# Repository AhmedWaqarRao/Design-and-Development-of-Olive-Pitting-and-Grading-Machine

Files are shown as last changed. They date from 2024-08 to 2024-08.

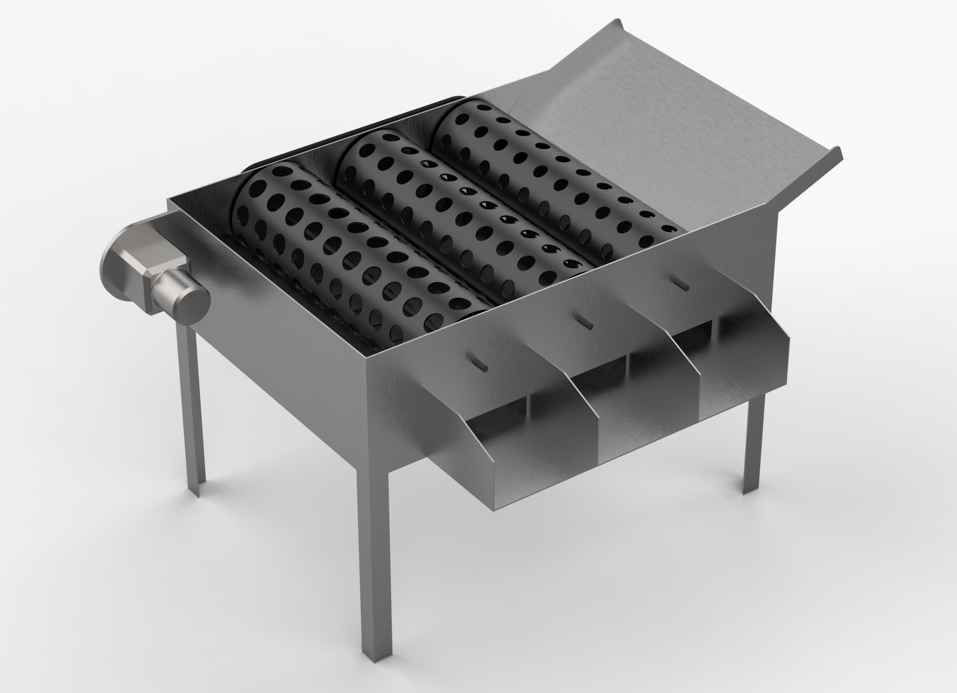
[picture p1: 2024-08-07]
Render 2 final design.png

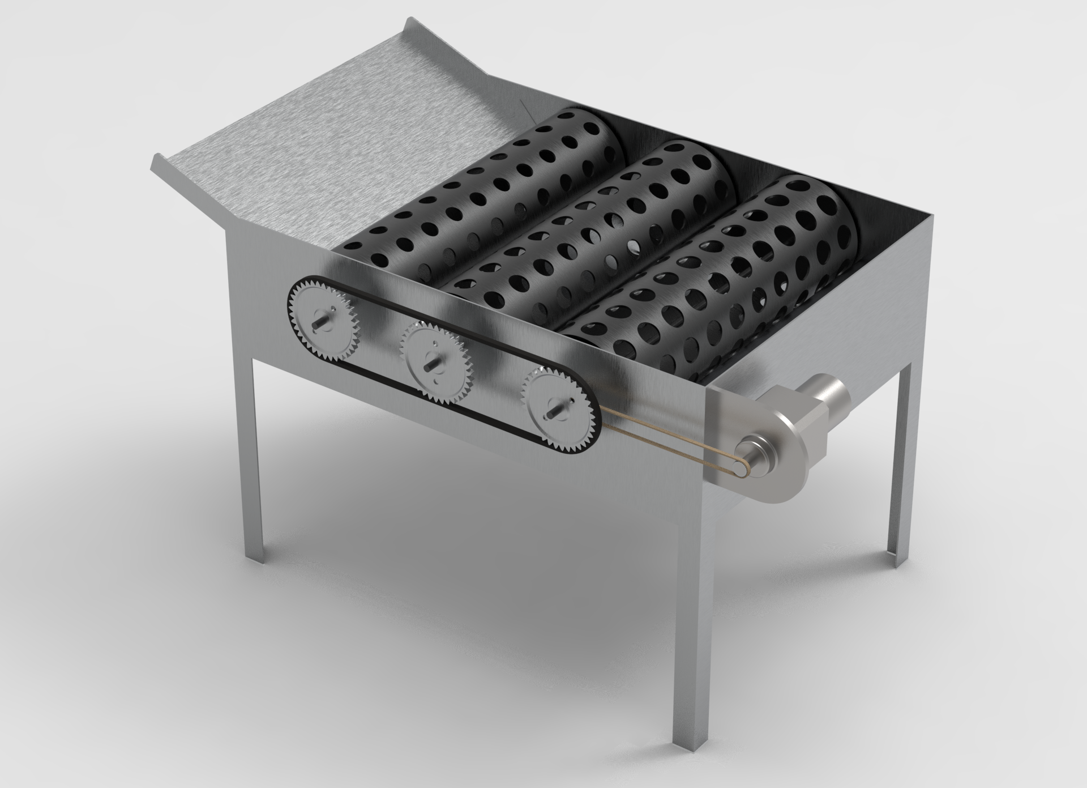
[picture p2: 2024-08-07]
Render final design 1.png

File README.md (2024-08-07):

# Design-and-Development-of-Olive-Pitting-and-Grading-Machine
An opportunity provides an effective mechanism for the purpose of the olives and removing pits from the
various varieties of olives cultivated in Pakistan. The project mainly focuses on the 3D model & hardware of
the Grading Mechanism of olives and the 3D CAD model of the pitting machine.75% of olive oil is imported
annually for domestic consumption.
The output will be a semi-automated machine that can grade and pit a number of olives at a time and has
an industrial and commercial approach.
A grading Mechanism will be used for the partition of different quality olives based on Olives.
Remove the seeds of olives when placed inside the Olive carrier drums along with the pins with the
help of two mechanisms.
i.e 1. Geneva Mechanism 2. Slider Crank Mechanism.

Final Year Project
— The invention in the technological world in Olive processing industry which increases the demand of the Olive industry. Olive pitting machine is mainly used for crushing and pitting of olives. The destoning of olive is the major area of concern in this project. A prototype is designed known as semi-autonomous machine for the extraction of olive and pitting process. Our Project is mainly focus on the Design of the Olive pitting Machine & Grading Machine. 
This machine will operate on no of mechanisms such as Geneva and slider crank mechanism. The assembly of machine is designed keeping in mind that all sizes of olives can be placed in one go on which pitting process need to be carried out. The major concern of our project lies in passing olives through fruit grading machine and then after this put that passed Olive into the Olive Pitting Machine whose task is to remove the seeds or pits of olives successfully the without damaging the outer part of the fruit.
 The project we have chosen for our FYP has both commercial and industrial value. The project holds to remove pit from olives mesh and then these olives can serve application in foods we are used on daily basis like tables olives, pickled olives and for extracting olives oil. Our area of target is to design a prototype whose specifications is grading olive one their sizes and destoning of pits.
I.	Introduction
Olive industry is growing day by day with the in interventions of technological solutions in olives process industry. The project holds to remove pit from olives mesh and then these olives can serve application in foods like tables olives and oil can also be extracted from the oils and is also used in pickels. We are to design a semi-automated machine whose function is to remove pit form olives [1].
There are 3 major parts in this semi-automated machine i.e., Olive feeder, Olive carrier, Pit detaching device. Olive feeder is the only semi-automatic part of the machine. In olive feeder olives need to be placed in such a way that it is in perfect contact with tip of needle and needle strike them longitudinally. 

Olive carrier is a revolving drum with sockets to hold various sizes of olives in predetermined position. The 24V motor is needed to rotate this drum and when needle encounter olive means when it strikes the olive then drum stop rotating. Pit detaching device consists of system of 9 needles which is capable of destoning 9 olives in just one go. The invention in the technological world in Olive processing industry which increases the demand of the Olive industry [3].

Olive pitting machine is mainly used for crushing and pitting of olives [2]. Our Project is mainly focus on the Design of the Olive pitting Machine & Grading Machine. The major objective of the of this project first to pass the olive through the Grading Machine and then after this put that passed Olive into the Olive Pitting Machine which successfully remove the pit of the olives without fracturing the outer part of the fruit [4]. The pitted Olive fruit can give us the income generating tool by making olive table oils, pickled olive and sliced or chopped olives can be use on pizza etc.

The Selected design of the Olive Extracting Machine resembles the cherry machine with modification in the driving mechanism having a Geneva Mechanism Crank-Slider Mechanism for the head of the device with a pitting needle. Holes of Rollers are selected according to the Grade of Olives needed to be pitted after being graded by the Olive Sorting Machine. 
The Pitting Machine Also includes Feeder and Collector Assembly for Feeding and collecting olives, respectively [5]. Mechanical System Based Olive Sorting: Mechanical based system for olive grading is the most used methodology. Mechanical Sorting Consists of Feeder Assembly through which olives are sent to conveyor belts arranged so that they are hollow from the bottom and carry the olives while moving forward.

II.	Methodology
Important paramteres and calculations
A.	DEVELOPMENT PHASE OF PITTING & GRADING MACHINE COMPONENT SPECIFICATIONS

	The overall parameters of the olive hopper, grading drums with holes; the length and diameters of drums, diameter and total number of holes and exit fall of the development grading-machine are included as follows.

B.	FINAL 3D CADCAM MODEL
This is the final achieved 3D CAD model of olive grading mechanism, after assembling all the parts. We entered the olives in 3 stages. First, we put 5kg of olives then 10kg and in 3rd stage we put 15kg of olives in the hopper, by 220 volts motor placed on the other side of the machine, the rolling drums starts to roll. 

Respective olives fall in 3 different categories according to their diameters which varies from 19mm diameter to 29mm.

After combining various mechanisms and components, the entire assembly of Olive Pit Extractor machine is obtained.
The shaft of the prime mover in the Geneva mechanism is connected to the crank in the slider crank mechanism.

The primary mover's wheel will be turned by an AC induction motor. The crank would generate rotational motion, which would be transformed into linear motion by the slider. The needle box is attached to the slider, and when linear motion is produced, the needle box moves along with the slider to conduct pitting operation.

 When the shaft of the prime mover catches on the slot of the driven wheel, it rotates the roller drum 45 degrees and aligns the roller drum sockets with those of the needle box for correct olive pitting.

Final 3d Cad Model Of Gradig Machine

Final 3d Cad Model Of pitting Machine

        C) Food Grading by Computer Vision:

In this modern era of industrialization, computer vision has become the most influential factor in revolutionizing the food industry. Food grading, including the size, orientation, Volume, weight, color, and checking the quality of a particular food type, has become very easy using computer vision. Machine Learning and Machine Vision make the perfect artificial intelligence system used for food processing. [10]

 1) Working:
 The most used Computer Vision Grading of Olives include    grading by Size and color. Modern image processing techniques are used to distinguish the difference in color and sizes. For imaging, High-Speed Cameras are used to capture images as fast as up to 120 frame rates.

 Data Acquisition Card (DAC) is used to control the system. Machine Learning is a must to process and compare the data to provide the best results. For color identification, Machine Learning techniques are used to easily differentiate between two colors that vary in intensities [11].

Figure : Olive Grading Machine Based on Machine Vision.

Figures : (a) Shows the machine’s interface (b) shows the high-speed cameras.

II.	SIMULATION ON ANSYS
To evaluate this design of machine it has been simulated and analyzed on different software named as Solid works and Ansys. Different set of analysis and constrained has been performed on machine.

A.	ANSYS SIMULATIONS:
1)	Static structural Analysis of Grading Machine:
Roller drum tis subjected to different simulations and the result shows that design of base of grading machine so strong and robust [6]. The Mild steel has Young Modulus of 2.10 x 10^9 pascal, which is used in manufacturing of needle. The poison ratio is 0.40 and mesh size is 20 mm .Following are the analysis run on this mechanism to test its robustness.

ANSYS software is used to perform analysis on different parts of grading machine. Force being applied on the bottom plate of the machine, pressure being applied on the rolling drums after olives are placed for grading and fixed supports of the machine, the figures are as below

                           Fixed Support             Force on the bottom plate

2)	Simulation by load of 50N:

      1) Directional and total deformation on x-axis:
A deformation option that displays all our model's deformation results in three coordinates (X, Y, and Z).  We can examine the deformation result of your physical model in this direction by entering a coordinate (X, Y, or Z) in directional deformation.

The directional deformation in x axis is applied on the roller drums. 50N load was applied. The results shows that the stress is high, but it doesn’t exceed certain limit. The pictorial representation of the result is shown below:

                             (1)                                               (2)
                      1) Directional Deformation in X axis – 50N  
                      2) Total Deformation – 50N

Von Mises Stress and elastic strain:
The drum is subjected to elastic strain and von misses stress are analyzed. 50N loads were applied to the drum. The results prove that drum is within limit and there are no chances that it will fracture. The following pictures shows the result carried out:
   
Analysis of Von-Mises Stress 50N  Analysis of Elastic Strain – 50N

3)	Roller Drum Carriers of Olives:
Roller drums are used for converting rotary motion to linear motion of fruit from the delivery plate. The coupler link was subjected to different simulations. The material for coupler is stainless steel and with Young Modulus of 2.10x10^7 pa. The mesh size is 20mm and   poison ratio is 0.40. Following are analysis run on roller drums and complete structure of grading machine shows its robustness.
B.	Output of Machine:
The olive pitting and grading machine is simulated in SOLID WORKS for motion analysis. The analysis shows that it is capable of grade 3 lines in 40 sec. We can conclude that machine is capable of grade 40-50kg of olives under certain conditions after analyzing the result.

C.	FRUITS:
We will be discussing 2 types of olive crops in this study: “Ascolana and Arbequina”. An approx. of 100 olives were used in our study. We collected the olive to be tested from the farms in Barani Agriculture Research Institute, Chakwal. Then the measurements were taken of the selected olives.
D.	GRADING-MACHINE: 
Following figures shows us the different parts being used in the grading machine, schematic diagrams help us to understand the parts of the grading machine.  The parameters depicted on the diagram are essentially those that will be determined for olives because of this investigation, to alter the grading machine to perform efficiently with this fruit [8].
 
Top view of assembled machine

Side view of assembled machine

            Designed Grading:
  		 1)  The Revolving Drums
Three revolving drums are made up of volcanized steel with following parameters: Diameter 92mm, length 305 mm, spacing 6mm, thickness 4mm. The three grading-drums have holes of diameters are 20-, 25- and 30-mm number of holes are 156, 137 and 124. 
Iron metal-sheet of 330mm length, 457 mm width and 1.5 mm (14 gauge) of thickness was assembled above grading-drums spacing and bolted on two sides of fruit boxes. 

2)  Fruit output unit
The output unit is made up of volcanized steel with length of 457mm and width of 127mm. Three fruit cutoffs were inserted into the three grading drums and fixed to the left side of the frame. The fruits slide down the concave surface of the output unit and fall into funnels. The curved section prevents fruits from being jammed. The inclined angle of output unit calculated is 12 degrees.

1)	Motor and Transmission System:
                     The grading system consists of 0.04 HP 	motor installed   and chains are given below:

 Chains side view of assembled machine

[1]
2)	1 Olive hopper:

The top dimensions are of 350 x 330 mm and bottom dimensions of 350 x 80 mm. The frictional angle made with the hopper and 1st drum is 30 degrees.
3)	2 Grading Drums:

The fruits are graded into three sizes using revolving drums. The diameter of the holes of the drum must be greater than the olives. 
The fruit > 30 mm exit from the end of the machine. As there are 3 grading drums for 3 different types of olives. Rotating/Grading drums and holes in it of varying diameter is 20mm. Length to accommodate 305 cm. 
The tangential angle of the drums in the fruit output direction must be more than 17 degree rolling angle between the olive fruits and the volcanized steel of grading machine. The tangential angle of the drums at the direction of drum motion is 7 degrees.

3 Olive output unit:
 The tangential angle of the drums of rolling angles between the olives and volcanized steel surface must be kept greater than 17 degrees.

E.	4 INSTRUMENTS INVOLVED IN THE PROCESS

1)	 Vernier Caliper
By the help of the Vernier Caliper with accuracy of 0.01mm we measured the different dimension of the olives.  

2)	 Digital balance
The accuracy of the digital balance is 0.2g it is used to measure the mass of the olives.

3)	 Graduated cylinder

For calculation of the density and volume of the olives by immerging in water of 1000ml with an accuracy of 25ml. 

4)	4 Friction and Rolling Angle Measuring Device 

An inclined plane was used to measure friction and rolling angles.
 	
I) Friction angle measurement 
The fruits are grouped together in a group on a horizontal surface, and the angle of inclination is progressively increased until the fruits begin to slide without rolling. Friction angles were calculated for each fruit group in a sample size of ten.

II) Rolling angle measurement

The fruits are placed one by one on flat plate, and the angle of elevation is progressively raised until the olives start rolling. Two rolling angles are calculated for each olive in an average sample (50).
F.	Studied factors and measurements
The development grading-machine variables investigated were:

1)	1 Grading speed:
Four different grading speeds 5, 8, 11 and 14 rpm (0.05, 0.08, 0.12 and 0.15 m/s).

2	Feeding rate: 
Four different feed rates of 5, 10, 15 and 20 kg. 
 
3 The Measurement were:
(1) Grading efficiency, 
(2) Fruit damage
(3) Grading productivity.

5	Equations and Calculations
2)		5.6.1 Sphericity Ratio
Sphericity ratio = fruit height (H) / fruit diameter (D) [10]
For olives: S.R = height / diameter
Table 1: Sphericity Ratio
Height (mm)	Diameter (mm)	Sphericity ratio
18.5	17.5	1.05
19.5	21.5	0.90
22.5	26.5	0.84

3)		5.6.2 Projected Area
	Projected area = 4/ (D * H)
Table 2: Projected Area
Height (mm)	Diameter (mm)	Projected area (mm²)
18.5	17.5	412.21
 19.5	21.5	533.08
22.5	26.5	759.16

4)	3 Real Density
		Real density = Mass / Volume; Volume = 4/3 (3.14)(r³)

Table 3: Real Density
No.	Mass (kg)	Volume (mm³)	Real Density (kg/mm³)
1	5	2758.33	0.0022
		3882.42	0.0013
		5694.12	0.0009
2	10	2758.33	0.0036
		3882.42	0.0025
		5694.12	0.0018
3	15	2758.33	0.0054
		3882.42	0.0038
		5694.12	0.0026

5)	4 Grading Productivity
According to; [11]

P = 3600 * M
      T

		P =   Grading Productivity (kg/h)
		M = Mass in sample (kg)
		T =   Time in seconds (s)

Table 4: Grading Productivity
Mass in sample (kg)	Time in seconds (s)	Grading Productivity (kg/h)
5	120	150
10	180	200
15	300	180

6)		5 Grading Efficiency
			
According to [14], the grading efficiency of each outlet was computed as follows.

 1 = M₀₁1/Mi1
 2 = M₀₂1/Mi1
 3 = M₀₃1/Mi1
 4 = M₀₄1/Mi1

Where:
	 u1, 2, 3 and 4: Grading efficiency of fruits for each outlet in the machine, (%).

                Mi1, Mi2, Mi3 and Mi4: Mass of each class inside olive hopper, (kg).

                  M₀₁, M₀₂, M₀₃ and M₀₄: Mass of olives for each outlet in the machine, (kg)

 6 Total Grading Efficiency:

             ‘T’ The total grading efficiency can be calculated by    the following equation:

                     = (1+ 2+ 3+ 4) / 4

            7 Mechanical damage

	Percentage of the mechanical damage was calculated by the following 	
		formula:
                    D.F   =      Nd / Nt x   100

	Where:

                       Nd0= No. of damaged olives
                       Nt0= Total olives

Table 5: Mechanical Damage
damaged olives	Total olives	D.F
25	100	25
28	80	35
35	75	46.67
	        
G.	7 Results and Discussions 
1)	1. Physical properties of olive fruits:
	
Dimensions, sphericity, mass, volume, actual density, and projected area of olive fruits are shown in Table 1. These statistics were collected on 100 fruit samples using the criteria established. [11]

2)	2. Dimensions of fruit

If the sphericity is less than 0.9; if the sphericity is larger than 1.1, the fruit is classified as oblong. Roundness is assumed for the remaining fruits with intermediate index values [12]	
The majority (85%) of olive in sample were round (sphericity 0.9 - 1.1), with oblong olive fruits accounting for 15% of the sample (sphericity 1.1 - 1.4).
III.	CONCLUSION
Our grading machine established a mechanism for grading and pitting of olive fruits that has vast applications as table oil and used for the extraction of olive’s oil. In addition to project our senior degree we have designed a grading prototype machine for sorting of olives on their sizes. 

The comparison of cost relative to other grading and pitting machines. The procedure we have carried out shows that olive pitting and grading machine holds importance both technically as well as from engineering point of view.

The importance of this machine is obvious from the fact provided that the production of such machines in Pakistan is non-existence due to lack of self-awareness and academic background. 

For pitting of olives, the slider cranks and Geneva mechanism is used but there are high chances of wear and tear of these components so there are utmost requirements of some modifications in this design. Also, in grading machine of olives there are also some errors carried out in making the holes of drum roller for sorting of olives. Some holes are big enough that olives pass through it without going through grading process.

The results we have carried out on this machine are given below:
The maximum fruit damage during pitting and grading process was 6.3 to 6.6%. This was obtained with the grading speed of 8.2rpm (0.08 m/s) and feeding rate of 19kg. With the grading speed of 11.1 rpm the minimum damage obtained was 3.2 to 3.4 % with the fruit size of 20mm and feeding rate of 6kg. The maximum range of grading machine productivity for olives of 112-835 was obtained with grading speed ranging from 6-15 rpm (0.06-0.16 m/s) and feeding rate was 19kg. 

The minimum range of grading machine productivity for olives fruits of 100-685 was obtained with grading speed of 5-14 rpm (0.06-0.15 m/s) and feeding rate of 5kg. The effective cost of our grading machine was from 38-40k.

 The advancement in the machine can made by converting it to fully automatic from semi-automatic machine. In this way labor effort and cost is reduced and high efficiency can be obtained. This advancement in the machine can serve as economic booster in country as there is high demand of olive’s oil.

IV.	ACKNOWLEDGMENT
We would like to thank our Supervisor, Dr. Hamid Jabbar and Co-Supervisor Dr. Umar Shahbaz for his insight, guidance and help in accomplishing this task. It has been a privilege to work under his supervision. We are grateful for his motivation and efforts that he gave us.  

Furthermore, we feel honored to have been taught by an excellent faculty and to have been graced with peers and friends without whom my pursuit of education would have been less gratifying.

These acknowledgments would not be complete without expressing our appreciations for my family whose continuous and firm support has enabled us to focus on our work without distraction.
We pray that Allah Almighty bestow upon them his blessings and bounties and continue to guide us in our future endeavors.

V.	REFERENCES

 	[1] F. J. Cimperman, "Machine for pitting and stuffing olives".Google patents. 
[2] T. Britannica, "Encyclopedia Britannia," Editors of Encyclopedia, 1 May 2019. [Online]. Available: https://www.britannica.com/plant/olive-plant. [Accessed 6 June 2022]. 
[3] Barani Chakwal Institute Management, "Barani Agriculture Reseacrh Institute," 5 June 2013. [Online]. Available: barichakwal.punjab.gov.pk/background. [Accessed 4 June 2022].
[4] F. P. M. TYQH-06, "THOYU," 5 MAY 2015. [Online]. Available: thoyu.com/ty-qh06- fruit-pitting-machine.html. [Accessed 1 DEC 2021].

[5] M. M. C. Ltd, "Miracle Machinery," 2 Sep 2016. [Online]. Available: http://www.mrcfoodmachine.com/fruits-processing-machinery/olive-processing machinery/automatic-olives-pitting-machine.html.

[6] E. G. M. G. H. J. U. S. Ahmed Faizan, "IEEE," June 2021. [Online]. Available: 
https://ieeexplore.ieee.org/abstract/document/9651337. [Accessed Jan 2021].

[7] PARC, "Pakistan Agriculture and Research council," 11 August 2014. [Online]. Available: http://www.parc.gov.pk/index.php/en/olive-history-of-olive-in-pakistan. [Accessed 6 June 2022].

[8] A. Lucas, "Deep learning in olive pitting machines by computer vision," 2018. [Online]. Available: sciencedirect.com/science/article/abs/pii/S0168169919310464. [Accessed 2022].

[9] T. E. o. E. Britannica, "Britannica," Britannica, [Online]. Available: https://www.britannica.com/technology/slider-crank-mechanism

[10] IOSR-JAVS, "Journal of Agriculture and Veterinary Science," Agriculture and Veterinary Science, vol. 9, no. 11, pp. 2319-2380, 2016.

[11] TRENT BULLOCK, "WHAT DOES "FOOD GRADE" MEAN?" Dec 2017. [Online]. Available: https://www.csidesigns.com/blog/articles/what-is-food-gra
de.

[12] El-Raie, A.E.; M.M. Attaullah; K. S. Khalil, "Factors affecting the design of a grading machine for lemon fruits,
Misr J. Ag. Eng., vol. 2, p. 29, 2012.

[13] Buyanov, A. I.; Voronyuk, B. A., Physical and mechanical properties of plants, fertilizers and Soils, New Delhi, Bombay, Calcutta: Amerind Pub. Co., PVT, LTD, 1985.

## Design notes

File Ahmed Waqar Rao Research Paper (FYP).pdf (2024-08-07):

# Design & Development of Olive pitting and Grading Machine

# Supervisors :

### Dr. Umar Shahbaz Khan Mechatronics Engineering NUST College of Electrical and Mechanical Engineering Islamabad, Pakistan u.shahbaz@ceme.nust.edu.pk

## Student :

### Ahmed Waqar Rao Mechatronics Engineering NUST College of Electrical and Mechanical Engineering Islamabad, Pakistan ahmedwaqarrao.909@gmail.c

om

### Dr. Hamid Jabbar Mechatronics Engineering NUST College of Electrical and Mechanical Engineering Islamabad, Pakistan hamid.jabbar@ceme.nust.edu

.pk

### Dr. Ameer Hamza Mechatronics Engineering NUST College of Electrical and Mechanical Engineering Islamabad, Pakistan a.hamza@ceme.nust.edu.pk

Abstract— the invention in the technological world in Olive

processing industry which increases the demand of the Olive industry. Olive pitting machine is mainly used for crushing and pitting of olives. The destoning of olive is the major area of concern in this project. A prototype is designed known as semi-autonomous machine for the extraction of olive and pitting process. Our Project is mainly focus on the Design of the Olive pitting Machine & Grading Machine.
This machine will operate on no of mechanisms such as Geneva and slider crank mechanism. The assembly of machine is designed keeping in mind that all sizes of olives can be placed in one go on which pitting process need to be carried out. The major concern of our project lies in passing olives through fruit grading machine and then after this put that passed Olive into the Olive Pitting Machine whose task is to remove the seeds or pits of olives successfully the without damaging the outer part of the fruit.
The project we have chosen for our FYP has both commercial and industrial value. The project holds to remove pit from olives mesh and then these olives can serve application in foods we are used on daily basis like tables olives, pickled olives and for extracting olives oil. Our area of target is to design a prototype whose specifications is grading olive one their sizes and destoning of pits.
I. Introduction

Olive industry is growing day by day with the in interventions of technological solutions in olives process industry. The project holds to remove pit from olives mesh and then these olives can serve application in foods like tables olives and oil can also be extracted from the oils and is also used in pickels. We are to design a semi-automated machine whose function is to remove pit form olives [1]. There are 3 major parts in this semi-automated machine i.e., Olive feeder, Olive carrier, Pit detaching device. Olive feeder is the only semi-automatic part of the machine. In olive feeder olives need to be placed in such a way that it is in perfect contact with tip of needle and needle strike them longitudinally.

Olive carrier is a revolving drum with sockets to hold various sizes of olives in predetermined position. The 24V motor is needed to rotate this drum and when needle encounter olive means when it strikes the olive then drum stop rotating. Pit detaching device consists of system of 9 needles which is capable of destoning 9 olives in just one go. The invention in the technological world in Olive processing industry which increases the demand of the Olive industry [3].

Olive pitting machine is mainly used for crushing and pitting of olives [2]. Our Project is mainly focus on the Design of the Olive pitting Machine & Grading Machine. The major objective of the of this project first to pass the olive through the Grading Machine and then after this put that passed Olive into the Olive Pitting Machine which successfully remove the pit of the olives without fracturing the outer part of the fruit [4]. The pitted Olive fruit can give us the income generating tool by making olive table oils, pickled olive and sliced or chopped olives can be use on pizza etc.

The Selected design of the Olive Extracting Machine resembles the cherry machine with modification in the driving mechanism having a Geneva Mechanism Crank-Slider Mechanism for the head of the device with a pitting needle. Holes of Rollers are selected according to the Grade

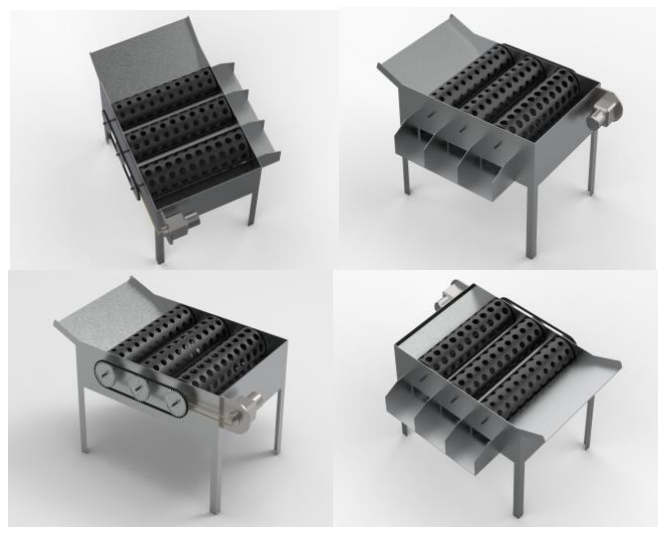
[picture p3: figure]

of Olives needed to be pitted after being graded by the Olive Sorting Machine.
The Pitting Machine Also includes Feeder and Collector Assembly for Feeding and collecting olives, respectively [5]. Mechanical System Based Olive Sorting: Mechanical based system for olive grading is the most used methodology. Mechanical Sorting Consists of Feeder Assembly through which olives are sent to conveyor belts arranged so that they are hollow from the bottom and carry the olives while moving forward.

II. Methodology

Important paramteres and calculations

A. DEVELOPMENT PHASE OF PITTING & GRADING MACHINE COMPONENT SPECIFICATIONS

The overall parameters of the olive hopper, grading drums with holes; the length and diameters of drums, diameter and total number of holes and exit fall of the development grading-machine are included as follows.

B. FINAL 3D CADCAM MODEL
This is the final achieved 3D CAD model of olive grading mechanism, after assembling all the parts. We entered the olives in 3 stages. First, we put 5kg of olives then 10kg and in 3rd stage we put 15kg of olives in the hopper, by 220 volts motor placed on the other side of the machine, the rolling drums starts to roll.

Respective olives fall in 3 different categories according to their diameters which varies from 19mm diameter to 29mm.

After combining various mechanisms and components, the entire assembly of Olive Pit Extractor machine is obtained. The shaft of the prime mover in the Geneva mechanism is connected to the crank in the slider crank mechanism.

The primary mover's wheel will be turned by an AC induction motor. The crank would generate rotational motion, which would be transformed into linear motion by the slider. The needle box is attached to the slider, and when linear motion is produced, the needle box moves along with the slider to conduct pitting operation.

When the shaft of the prime mover catches on the slot of the driven wheel, it rotates the roller drum 45 degrees and aligns the roller drum sockets with those of the needle box for correct olive pitting.

Final 3d Cad Model Of Gradig Machine

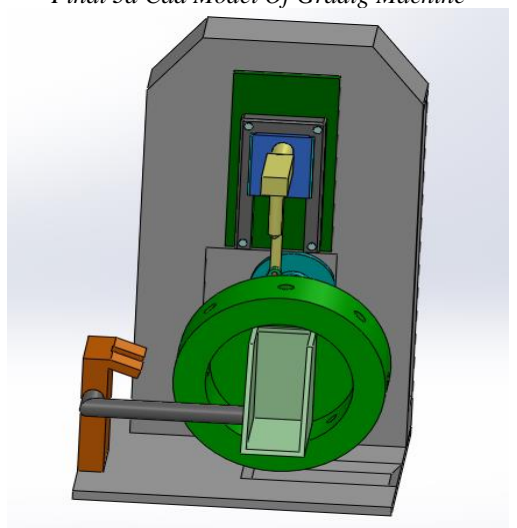
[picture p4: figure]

Final 3d Cad Model Of pitting Machine

### C) Food Grading by Computer Vision:

In this modern era of industrialization, computer vision has become the most influential factor in revolutionizing the food industry. Food grading, including the size, orientation, Volume, weight, color, and checking the quality of a particular food type, has become very easy using computer vision. Machine Learning and Machine Vision make the perfect artificial intelligence system used for food processing. [10]

### 1) Working:

The most used Computer Vision Grading of Olives include grading by Size and color. Modern image processing techniques are used to distinguish the difference in color and sizes. For imaging, High-Speed Cameras are used to capture images as fast as up to 120 frame rates.

Data Acquisition Card (DAC) is used to control the system. Machine Learning is a must to process and compare the data to provide the best results. For color identification, Machine Learning techniques are used to easily differentiate between two colors that vary in intensities [11].

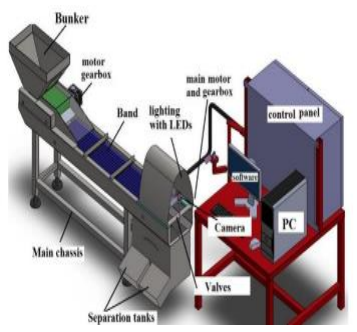
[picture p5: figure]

Figure : Olive Grading Machine Based on Machine Vision.

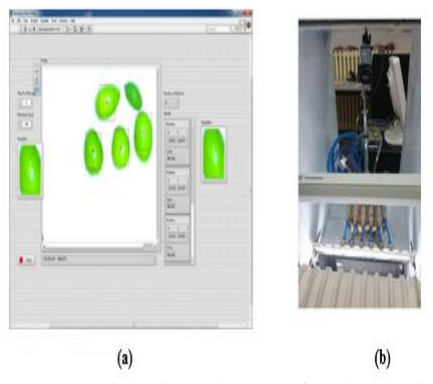
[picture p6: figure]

Figures : (a) Shows the machine’s interface (b) shows the high-speed cameras.

II.SIMULATION ON ANSYS
To evaluate this design of machine it has been simulated and analyzed on different software named as Solid works and Ansys. Different set of analysis and constrained has been performed on machine.
A. ANSYS SIMULATIONS:
1) Static structural Analysis of Grading Machine: Roller drum tis subjected to different simulations and the result shows that design of base of grading machine so strong and robust [6]. The Mild steel has Young Modulus of 2.10 x 10^9 pascal, which is used in manufacturing of needle. The poison ratio is 0.40 and mesh size is 20 mm .Following are the analysis run on this mechanism to test its robustness.

ANSYS software is used to perform analysis on different parts of grading machine. Force being applied on the bottom plate of the machine, pressure being applied on the rolling drums after olives are placed for grading and fixed supports of the machine, the figures are as below

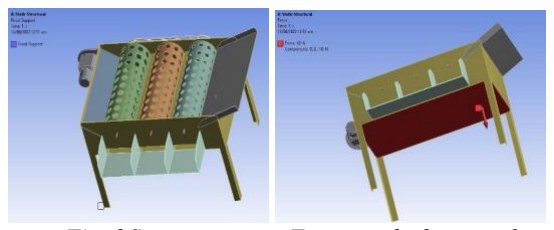
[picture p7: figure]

Fixed Support | Force on the bottom plate
2) Simulation by load of 50N:
1) Directional and total deformation on x-axis:
A deformation option that displays all our model's deformation results in three coordinates (X, Y, and Z). We can examine the deformation result of your physical model in this direction by entering a coordinate (X, Y, or Z) in directional deformation.

The directional deformation in x axis is applied on the roller drums. 50N load was applied. The results shows that the stress is high, but it doesn’t exceed certain limit. The pictorial representation of the result is shown below:

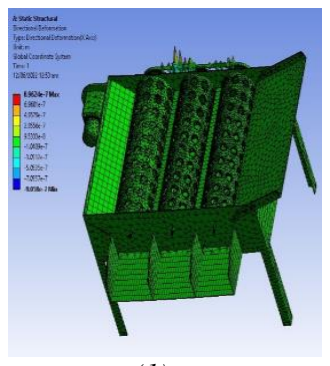
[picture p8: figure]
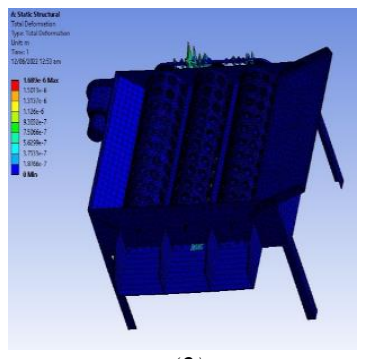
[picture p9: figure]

(1) (2)
1) Directional Deformation in X axis – 50N
2) Total Deformation – 50N

Von Mises Stress and elastic strain: The drum is subjected to elastic strain and von misses stress are analyzed. 50N loads were applied to the drum. The results prove that drum is within limit and there are no chances that it will fracture. The following pictures shows the result carried out:

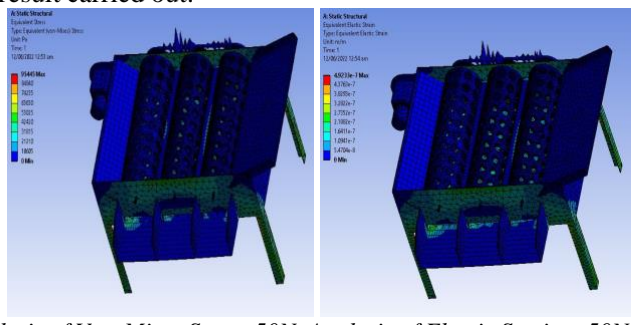
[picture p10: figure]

Analysis of Von-Mises Stress 50N Analysis of Elastic Strain – 50N

3) Roller Drum Carriers of Olives: Roller drums are used for converting rotary motion to linear motion of fruit from the delivery plate. The coupler link was subjected to different simulations. The material for coupler is stainless steel and with Young Modulus of 2.10x10^7 pa. The mesh size is 20mm and poison ratio is 0.40. Following are analysis run on roller drums and complete structure of grading machine shows its robustness.
B. Output of Machine:
The olive pitting and grading machine is simulated in
SOLID WORKS for motion analysis. The analysis shows that it is capable of grade 3 lines in 40 sec. We can conclude that machine is capable of grade 40-50kg of olives under certain conditions after analyzing the result.
C. FRUITS:
We will be discussing 2 types of olive crops in this study: “Ascolana and Arbequina”. An approx. of 100 olives were used in our study. We collected the olive to be tested from the farms in Barani Agriculture Research Institute, Chakwal. Then the measurements were taken of the selected olives.
D. GRADING-MACHINE:
Following figures shows us the different parts being used in the grading machine, schematic diagrams help us to understand the parts of the grading machine. The parameters depicted on the diagram are essentially those that will be determined for olives because of this investigation, to alter the grading machine to perform efficiently with this fruit [8].

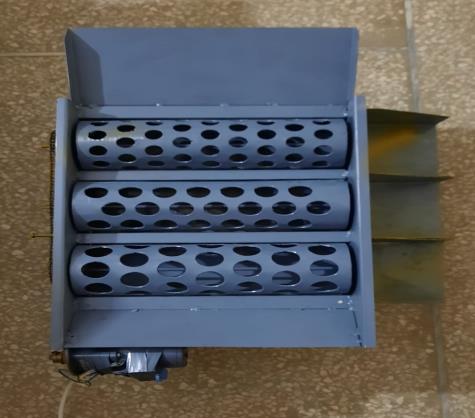
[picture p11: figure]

Top view of assembled machine

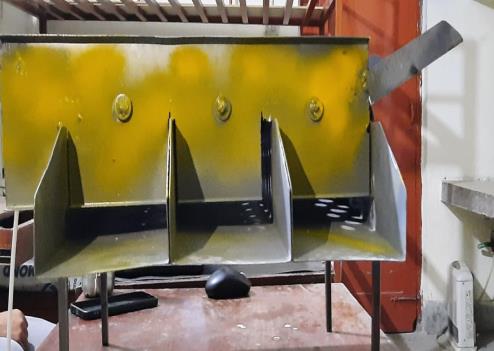
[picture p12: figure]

Side view of assembled machine

Designed Grading:

1) The Revolving Drums
Three revolving drums are made up of volcanized steel with following parameters: Diameter 92mm, length 305 mm, spacing 6mm, thickness 4mm. The three grading-drums have holes of diameters are 20-, 25- and 30-mm number of holes are 156, 137 and 124.
Iron metal-sheet of 330mm length, 457 mm width and 1.5 mm (14 gauge) of thickness was assembled above grading-drums spacing and bolted on two sides of fruit boxes.
2) Fruit output unit
The output unit is made up of volcanized steel with length of 457mm and width of 127mm. Three fruit cutoffs were inserted into the three grading drums and fixed to the left side of the frame. The fruits slide down the concave surface of the output unit and fall into funnels. The curved section prevents fruits from being jammed. The inclined angle of output unit calculated is 12 degrees.

1) Motor and Transmission System:
The grading system consists of 0.04 HP motor installed and chains are given below:

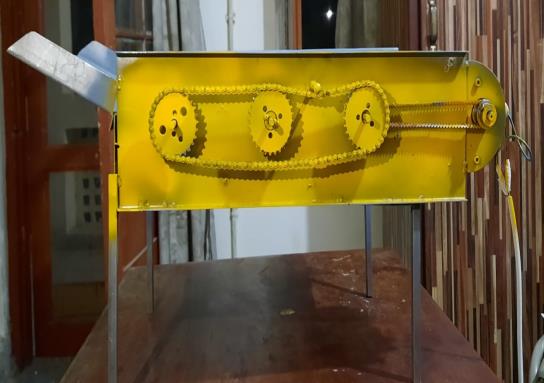
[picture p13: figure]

Chains side view of assembled machine

[1]
2) 1 Olive hopper:

The top dimensions are of 350 x 330 mm and bottom dimensions of 350 x 80 mm. The frictional angle made with the hopper and 1st drum is 30 degrees.
3) 2 Grading Drums:

The fruits are graded into three sizes using revolving drums. The diameter of the holes of the drum must be greater than the olives.
The fruit > 30 mm exit from the end of the machine. As there are 3 grading drums for 3 different types of olives. Rotating/Grading drums and holes in it of varying diameter is 20mm. Length to accommodate 305 cm.
The tangential angle of the drums in the fruit output direction must be more than 17 degree rolling angle between the olive fruits and the volcanized steel of grading machine. The tangential angle of the drums at the direction of drum motion is 7 degrees.

3 Olive output unit:
The tangential angle of the drums of rolling angles between the olives and volcanized steel surface must be kept greater than 17 degrees.
E. 4 INSTRUMENTS INVOLVED IN THE PROCESS
1) Vernier Caliper
By the help of the Vernier Caliper with accuracy of 0.01mm we measured the different dimension of the olives.
2) Digital balance
The accuracy of the digital balance is 0.2g it is used to measure the mass of the olives.
3) Graduated cylinder

For calculation of the density and volume of the olives by immerging in water of 1000ml with an accuracy of 25ml.

4) 4 Friction and Rolling Angle Measuring Device

An inclined plane was used to measure friction and rolling angles.

I) Friction angle measurement
The fruits are grouped together in a group on a horizontal surface, and the angle of inclination is progressively increased until the fruits begin to slide without rolling. Friction angles were calculated for each fruit group in a sample size of ten.

II) Rolling angle measurement

The fruits are placed one by one on flat plate, and the angle of elevation is progressively raised until the olives start rolling. Two rolling angles are calculated for each olive in an average sample (50).

F. Studied factors and measurements
The development grading-machine variables investigated were:
1) 1 Grading speed:
Four different grading speeds 5, 8, 11 and 14 rpm (0.05, 0.08, 0.12 and 0.15 m/s).

2 Feeding rate:
Four different feed rates of 5, 10, 15 and 20 kg.
| 3 The Measurement were:
(1) Grading efficiency,
(2) Fruit damage
(3) Grading productivity.

### 5 Equations and Calculations

2) 5.6.1 Sphericity Ratio
Sphericity ratio = fruit height (H) / fruit diameter (D) [10]
For olives: S.R = height / diameter
Table 1: Sphericity Ratio
Height (mm) | Diameter (mm) | Sphericity ratio
18.5 | 17.5 | 1.05
19.5 | 21.5 | 0.90
22.5 | 26.5 | 0.84
3) 5.6.2 Projected Area
Projected area = 4/π (D * H)
Table 2: Projected Area
Height (mm) | Diameter (mm) | Projected area (mm²)
18.5 | 17.5 | 412.21
19.5 | 21.5 | 533.08

22.5 | 26.5 | 759.16
4) 3 Real Density
Real density = Mass / Volume; Volume = 4/3 (3.14)(r³)

Table 3: Real Density
No. | Mass (kg) | Volume (mm³) | Real Density (kg/mm³)
1 | 5 | 2758.33 | 0.0022
| | 3882.42 | 0.0013
| | 5694.12 | 0.0009
2 | 10 | 2758.33 | 0.0036
| | 3882.42 | 0.0025
| | 5694.12 | 0.0018
3 | 15 | 2758.33 | 0.0054
| | 3882.42 | 0.0038
| | 5694.12 | 0.0026
5) 4 Grading Productivity
According to; [11]

P = 3600 * M
T

P = Grading Productivity (kg/h) M = Mass in sample (kg)
T = Time in seconds (s)

Table 4: Grading Productivity

Mass in sample (kg) | Time in seconds (s) | Grading Productivity (kg/h)
5 | 120 | 150
10 | 180 | 200
15 | 300 | 180
6) 5 Grading Efficiency

According to [14], the grading efficiency of each outlet was computed as follows.

µ 1 = M₀₁1/Mi1
µ 2 = M₀₂1/Mi1
µ 3 = M₀₃1/Mi1
µ 4 = M₀₄1/Mi1

Where:

u1, µ2, µ3 and µ4: Grading efficiency of fruits for each outlet in the machine, (%).

Mi1, Mi2, Mi3 and Mi4: Mass of each class inside olive hopper, (kg).

M₀₁, M₀₂, M₀₃ and M₀₄: Mass of olives for each outlet in the machine, (kg)

6 Total Grading Efficiency:

‘T’ The total grading efficiency can be calculated by the following equation:

µ = (µ1+ µ2+ µ3+ µ4) / 4

7 Mechanical damage

Percentage of the mechanical damage was calculated by the following
formula:
D.F = Nd / Nt x 100

Where:

Nd0= No. of damaged olives Nt0= Total olives

Table 5: Mechanical Damage
damaged olives | Total olives | D.F
25 | 100 | 25
28 | 80 | 35
35 | 75 | 46.67
G. 7 Results and Discussions
1) 1. Physical properties of olive fruits:

Dimensions, sphericity, mass, volume, actual density, and projected area of olive fruits are shown in Table 1. These statistics were collected on 100 fruit samples using the criteria established. [11]

2) 2. Dimensions of fruit

If the sphericity is less than 0.9; if the sphericity is larger than 1.1, the fruit is classified as oblong. Roundness is assumed for the remaining fruits with intermediate index values [12]
The majority (85%) of olive in sample were round (sphericity 0.9 - 1.1), with oblong olive fruits accounting for 15% of the sample (sphericity 1.1 -1.4).

III.CONCLUSION
Our grading machine established a mechanism for grading and pitting of olive fruits that has vast applications as table oil and used for the extraction of olive’s oil. In addition to project our senior degree we have designed a grading prototype machine for sorting of olives on their sizes.

The comparison of cost relative to other grading and pitting machines. The procedure we have carried out shows that olive pitting and grading machine holds importance both technically as well as from engineering point of view.

The importance of this machine is obvious from the fact provided that the production of such machines in Pakistan is non-existence due to lack of self-awareness and academic background.

For pitting of olives, the slider cranks and Geneva mechanism is used but there are high chances of wear and tear of these components so there are utmost requirements of some modifications in this design. Also, in grading machine of olives there are also some errors carried out in making the holes of drum roller for sorting of olives. Some holes are big enough that olives pass through it without going through grading process.

The results we have carried out on this machine are given below:
The maximum fruit damage during pitting and grading process was 6.3 to 6.6%. This was obtained with the grading speed of 8.2rpm (0.08 m/s) and feeding rate of 19kg. With the grading speed of 11.1 rpm the minimum damage obtained was 3.2 to 3.4 % with the fruit size of 20mm and feeding rate of 6kg. The maximum range of grading machine productivity for olives of 112-835 was obtained with grading speed ranging from 6-15 rpm (0.06-0.16 m/s) and feeding rate was 19kg.

The minimum range of grading machine productivity for olives fruits of 100-685 was obtained with grading speed of 5-14 rpm (0.06-0.15 m/s) and feeding rate of 5kg. The effective cost of our grading machine was from 38-40k.

The advancement in the machine can made by converting it to fully automatic from semi-automatic machine. In this way labor effort and cost is reduced and high efficiency can be obtained. This advancement in the machine can serve as economic booster in country as there is high demand of olive’s oil.

IV.ACKNOWLEDGMENT
We would like to thank our Supervisor, Dr. Hamid Jabbar and Co-Supervisor Dr. Umar Shahbaz for his insight, guidance and help in accomplishing this task. It has been a privilege to work under his supervision. We are grateful for his motivation and efforts that he gave us.

Furthermore, we feel honored to have been taught by an excellent faculty and to have been graced with peers and friends without whom my pursuit of education would have been less gratifying.

These acknowledgments would not be complete without expressing our appreciations for my family whose continuous and firm support has enabled us to focus on our work without distraction.
We pray that Allah Almighty bestow upon them his blessings and bounties and continue to guide us in our future endeavors.

V.REFERENCES

[1] F. J. Cimperman, "Machine for pitting and stuffing olives".Google patents.
[2] T. Britannica, "Encyclopedia Britannia," Editors of Encyclopedia, 1 May 2019. [Online]. Available: https://www.britannica.com/plant/olive-plant. [Accessed 6 June 2022].
[3] Barani Chakwal Institute Management, "Barani Agriculture Reseacrh Institute," 5 June 2013. [Online]. Available: barichakwal.punjab.gov.pk/background. [Accessed 4 June 2022].
[4] F. P. M. TYQH-06, "THOYU," 5 MAY 2015. [Online]. Available: thoyu.com/ty-qh06- fruit-pitting-machine.html.

[Accessed 1 DEC 2021].

[5] M. M. C. Ltd, "Miracle Machinery," 2 Sep 2016. [Online]. Available: http://www.mrcfoodmachine.com/fruits-processing-machinery/olive-processing machinery/automatic-olives-pitting-machine.html.
[6] E. G. M. G. H. J. U. S. Ahmed Faizan, "IEEE," June 2021. [Online]. Available:
https://ieeexplore.ieee.org/abstract/document/9651337. [Accessed Jan 2021].
[7] PARC, "Pakistan Agriculture and Research council," 11 August 2014. [Online]. Available: http://www.parc.gov.pk/index.php/en/olive-history-of-olive-in-pakistan. [Accessed 6 June 2022].
[8] A. Lucas, "Deep learning in olive pitting machines by computer vision," 2018. [Online]. Available: sciencedirect.com/science/article/abs/pii/S0168169919310464. [Accessed 2022].
[9] T. E. o. E. Britannica, "Britannica," Britannica, [Online]. Available: https://www.britannica.com/technology/slider-crank-mechanism
[10] IOSR-JAVS, "Journal of Agriculture and Veterinary Science," Agriculture and Veterinary Science, vol. 9, no. 11, pp. 2319-2380, 2016.
[11] TRENT BULLOCK, "WHAT DOES "FOOD GRADE" MEAN?" Dec 2017. [Online]. Available: https://www.csidesigns.com/blog/articles/what-is-food-gra de.
[12] El-Raie, A.E.; M.M. Attaullah; K. S. Khalil, "Factors affecting the design of a grading machine for lemon fruits, Misr J. Ag. Eng., vol. 2, p. 29, 2012.
[13] Buyanov, A. I.; Voronyuk, B. A., Physical and mechanical properties of plants, fertilizers and Soils, New Delhi, Bombay, Calcutta: Amerind Pub. Co., PVT, LTD, 1985.

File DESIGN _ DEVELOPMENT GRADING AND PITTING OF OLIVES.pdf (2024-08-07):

DE-40 (MTS-A) S.M. SAIM NAVAID, M. OSAMA GUL, AHMED WAQAR RAO

DESIGN AND DEVELOPMENT OF OLIVE PITTING & GRADING MACHINE

COLLEGE OF
ELECTRICAL AND MECHANICAL ENGINEERING NATIONAL UNIVERSITY OF SCIENCES AND TECHNOLOGY RAWALPINDI 2022

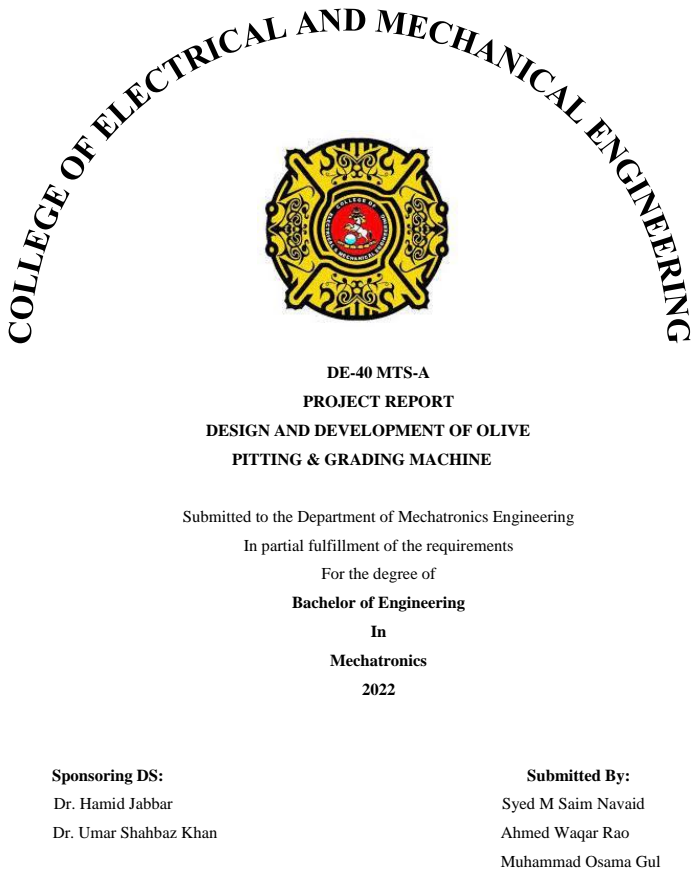
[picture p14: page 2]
DE-40 MTS-A; PROJECT REPORT; Mechatronics; Sponsoring DS:; Submitted By:; Dr. Hamid Jabbar; Syed M Saim Navaid; Dr. Umar Shahbaz Khan; Ahmed Waqar Rao

DESIGN AND DEVELOPMENT OF OLIVE

PITTING & GRADING MACHINE

Submitted to the Department of Mechatronics Engineering

In partial fulfillment of the requirements

For the degree of

Bachelor of Engineering

Muhammad Osama Gul

ACKNOWLEDGMENTS

We would like to thank our Supervisor, Dr. Hamid Jabbar and Co-Supervisor Dr. Umar Shahbaz

for his insight, guidance and help in accomplishing this task. It has been a privilege to work under

his supervision. We are grateful for his motivation and efforts that he gave us.

Furthermore we feel honored to have been taught by an excellent faculty and to have been graced

with peers and friends without whom my pursuit of education would have been less gratifying.

These acknowledgments would not be complete without expressing our appreciations for my family

whose continuous and firm support has enabled us to focus on our work without distraction.

We pray that Allah Almighty bestow upon them his blessings and bounties and continue to guide

us in our future endeavors.

THANK YOU.

ABSTRACT

The invention in the technological world in Olive processing industry which increases the

demand of the Olive industry. Olive pitting machine is mainly used for crushing and pitting of

olives. The destoning of olive is the major area of concern in this project. A prototype is

designed known as semi-autonomous machine for the extraction of olive and pitting process.

Our Project is mainly focus on the Design of the Olive pitting Machine & Grading Machine.

This machine will operate on no of mechanisms such as Geneva and slider crank mechanism.

The assembly of machine is designed keeping in mind that all sizes of olives can be placed in

one go on which pitting process need to be carried out. The major concern of our project lies

in passing olives through fruit grading machine and then after this put that passed Olive into

the Olive Pitting Machine whose task is to remove the seeds or pits of olives successfully the

without damaging the outer part of the fruit. The project we have chosen for our FYP has both

commercial and industrial value. The project holds to remove pit from olives mesh and then

these olives can serve application in foods we are used on daily basis like tables olives, pickled

olives and for extracting olives oil. Our area of target is to design a prototype whose

specifications is grading olive one their sizes and destoning of pits.

TABLE OF CONTENTS

ACKNOWLEDGMENTS | 4
ABSTRACT | 2
TABLE OF CONTENTS | 3
LIST OF TABLES | 7
CHAPTER 1: INTRODUCTION | 1
CHAPTER 2: LITERATURE REVIEW | 4
2.1.1 | Varieties of Olives in Pakistan | 5
2.2 | OLIVE SELECTION FOR PROJECT | 10
2.3 | EXISTING OLIVE PITTING MACHINE DESIGNS | 11
2.3.1 | Machine Having Belt with Horizontal Punching: | 11
2.3.2 | Machine Having Belt with Vertical Punching: | 12
2.3.3 | Vertical Punching Machine with Circular Feed Plate: | 12
2.4 | SELECTED DESIGN FOR PITTING MACHINE | 13
2.5 | VARIOUS PARTS OF OLIVE PITTING MACHINE | 14
2.5.1 | Olive Feeder: | 14
2.5.2 | Olive Carrier: | 14
2.2.3 | Pit Detaching Device: | 14
2.6 | MECHANISMS USED IN OLIVE PITTING MACHINE | 14
2.6.1 | Slider Crank Mechanism | 15
2.6.2 | Geneva Mechanism: | 16
2.7 | SOME PREPROCESSING FOR OLIVES | 17
2.8 | GRADING/ SORTING OF OLIVES | 17
2.8.1 | Food Grading by Machine Vision: | 18
2.8.2 | Mechanical System Based Olive Sorting: | 19
2.9 | FOOD-GRADE MATERIALS | 20
2.9.1 | Food Grade Metals: | 21
CHAPTER 3: DESIGNING OLIVE PITTING MACHINE | 23
3.1 DESIGN OF OLIVE PITTING MACHINE: | 23
3.2 COMPONENTS OF THE MACHINE: | 23
3.2.1 Roller Drum: | 24

5.3 DEVELOPMENT PHASES AND GRADING MACHINE COMPONENT

LIST OF TABLES

CHAPTER 1: INTRODUCTION

Olives play significant role in dietary and for medical purposes all around the world. According

to a survey it is estimated that global olive market is projected to reach 17.2 billion dollars by

end of 2028. Pakistan has 10 million acres of land for olive production. Olive industry is

growing day by day with the in interventions of technological solutions in olives process

industry. The one of most important process is removal of pit from olives which is also our

required goal. There are two procedures for destoning of olives i.e.

- Partial destoning
- Total destoning

The project we have chosen for our FYP has both commercial and industrial value. The project

holds to remove pit from olives mesh and then these olives can serve application in foods like

tables olives and oil can also be extracted from the oils and is also used in pickels.

We are to design a semi automated machine whose function is to remove pit form olives. This

machine will operate on no of mechanisms such as Geneva and slider crank mechanism. All

size of olives can be placed in holes through which pitting needed to be performed [1]. There

are 3 major parts in this semi-automated machine i.e.

- Olive feeder
- Olive carrier
- Pit detaching device

Olive feeder is the only semi-automatic part of the machine. In olive feeder olives need to be

placed in such a way that it is in perfect contact with tip of needle and needle strike them

longitudinally.

Olive carrier is a revolving drum with sockets to hold various sizes of olives in predetermined

position. The 24V motor is needed to rotate this drum and when needle encounter olive means

when it strikes the olive then drum stop rotating. Usually, the sockets are designed in such way to accommodate 72 olives at one instance. Mainly our goal is to cater destoning of two types

of olives i.e., Arbequina and Ascolana.

Pit detaching device consists of system of 9 needles which is capable of destoning 9 olives in

just one go. The device is based on phenomena known as Geneva Mechanism. The device is

designed in such a way that effective, and accuracy is obtained in destoning of olives. The one

thing is to keep in mind that needle should not damage the olives or itself while pitting process.

After destoning the olive’s flesh and seed is collected at different points. The invention in the

technological world in Olive processing industry which increases the demand of the Olive

industry. Olive pitting machine is mainly used for crushing and pitting of olives. Pit removal

is a major constraint in processing.

A semi-autonomous machine is designed for effective pit extraction. Our Project is mainly

focus on the Design of the Olive pitting Machine & Grading Machine. The major objective of

the of this project first to pass the olive through the Grading Machine and then after this put

that passed Olive into the Olive Pitting Machine which successfully remove the pit of the olives

without fracturing the outer part of the fruit.

The pitted Olive fruit can give us the income generating tool by making olive table oils, pickled

olive and sliced or chopped olives can be use on pizza etc. The Selected design of the Olive

Extracting Machine resembles the cherry machine with modification in the driving mechanism

having a Geneva Mechanism Crank-Slider Mechanism for the head of the device with a pitting

needle.

The machine is driven by a 24 Volts DC-powered Motor, making it autonomous. Holes of

Rollers are selected according to the Grade of Olives needed to be pitted after being graded by

the Olive Sorting Machine. The Pitting Machine Also includes Feeder and Collector Assembly

for Feeding and collecting olives, respectively.

Mechanical System Based Olive Sorting: Mechanical based system for olive grading is the

most used methodology. This system works based on conveyor belts and sorts the olives

according to their sizes which can be further sent for processing.

Mechanical Sorting Consists of Feeder Assembly through which olives are sent to conveyor

belts arranged so that they are hollow from the bottom and carry the olives while moving

forward. The carrier is designed so that the initial distance between the two compartments is

less and increasing as it moves forward. The olives fell according to their size and are collected

using a collector assembled below the belt.

Problems & Shortcomings in the Previous Design:

- No Testing of olives on Machine was performed because Season was over.
- No Grading Mechanism
- Pin Configuration
- Food Grade Material

A new Enhanced working Olive pitting Machine & Grading Machine will be delivered in our

project.

CHAPTER 2: LITERATURE REVIEW

Olives are found in central Tropical, Asia, and Mediterranean tropical and in different regions

of Africa. It has also become an emblem of Greek heritage in the modern world. The olive tree

is one of the most treasured and sacred trees among Greeks, and its significance is deeply

established in Greek mythology and history [1]. Olives are far too bitter to consume raw and

can only be relished after treatment, usually curing or pickling. Most olives are turned into

olive oil, although some are preserved and used in dishes, mainly Mediterranean cuisine.

Olives roughly provide about 115 to 145 calories per 100 grams or 59 calories per 10 olives.

Because of their high lipid content, olives are a unique fruit. Oleic acid is the most prevalent

fat in it, and it may offer various health benefits. They also contain 4–6% carbohydrates, the

majority of which is fiber. Vitamin E, iron, copper, and calcium are all abundant in olives. If

wrapped in saltwater, they could have much sodium in them [2].

Olives are high in antioxidants, which may help with many health benefits like lowering

cholesterol, which helps prevent heart diseases and blood pressure. They may also reduce your

cancer and bone loss risks [2]. Olives are used in the medicine and textile industry and for

manufacturing high-quality cooking oil for kitchen uses.

### 2.1 OLIVES IN PAKISTAN

Although Pakistan is not famous for its olive production, a wild subspecies of the olive

tree known as 'Olea cuspidate' grows in various parts. The environment in Pakistan is

ideal for developing olive trees since they grow quickly and thrive in the mild winters

that follow a long hot summer [3].

Figure 1: Existing olive plantation in Pakistan.

There are more than ten varieties of olives are being cultivated in different regions of

Pakistan. Both Soil and Environmental factors are very suitable for the large-scale

cultivation of olives in Pakistan, including the mountainous areas such as Balochistan.

The most favorable regions to olive cultivation include Killah Saifullah, Zhob,

Chakwal, Musakhali, Khuzdar, Potohar Regions, and the various areas of Balochistan

and KPK. [4]

### 2.1.1 Varieties of Olives in Pakistan

The Top 12 Varieties of olives in Pakistan include Koroneiki, Arbequina,

Pendolino, Jerboui, Earlik, Hamdi, Manzanilla, Ascolana, Hojiblanca, Gemlik,

Pecual, chemlali [5].

1) Koroneiki

This type has medium vigor and erect branches, and it ripens in October.

The fruit is small (0.93g) and is used to extract oil. Fruit yields average

18-22 kg per plant, with a 16.22% oil recovery rate.

Figure 2: Koroneki.Olives

2) Arbequina

This type has medium vigor and erect branches, and it ripens in October.

The fruit is small (1.87 g), and it is used to extract oil. Fruit yields

average is 20-25 kg per plant, with a 15-18% oil recovery rate.

Figure 3: Arbequina Olive.

3) Pendolino

This type has strong vigor and spreading branches, and it ripens in

September. The fruit is small (1.72 g), and it is used to extract oil. Fruit

yields average is 25-35 kg per plant, with a 20% oil recovery rate.

Figure 4: Pendolina Olive.

4) Earlik

This type has weak vigor and spreading branches, and it ripens in

October. The fruit is Large (3.45 g), and it is used to extract oil and table

use. Fruit yields average is 30-35 kg per plant, with a 16-17% oil

recovery rate.

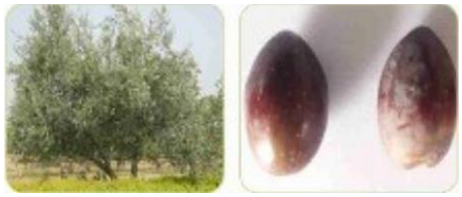
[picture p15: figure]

Figure 5: Earlik Olive

5) Hamdi

This type has weak vigor and drooping branches, and it ripens in

September-October. The fruit is medium (3.67 g), and it is used for table

products. Fruit yields average is 25-30 kg per plant, with a 15-17% oil

recovery rate.

Figure 6: Hamdi Olive.

6) Manzanilla

This type has weak vigor and spreading branches, and it ripens in

September-October. The fruit is large (4.60 g), and it is used to extract

oil. Fruit yields average is 20-25 kg per plant, with a 15-17% oil

recovery rate.

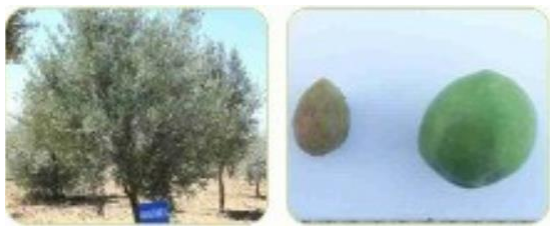
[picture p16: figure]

Figure 7: Maznzanilla Olive.

7) Ascolana

This type has strong vigor and spreading cum erect branches, and it

ripens in October. The fruit is large (4.56 g), and it is used to extract oil

and table use. Fruit yields average is 20-25 kg per plant, with a 14-15%

oil recovery rate.

Figure 8: Ascolana Olive.

8) Jerboui

This type has medium vigor and spreading branches, and it ripens in

September. The fruit is medium (2.80 g), and it is used to extract oil.

Fruit yields average is 20-24 kg per plant, with a 20-21% oil recovery

rate.

Figure 9: Jerboui Olive.

9) Hojiblanca

This type has medium vigor and spreading branches, and it ripens in

September-October. The fruit is medium (4.1 g), and it is used to extract

oil and table use. Fruit yields average is 22-26 kg per plant, with a 16-

18% oil recovery rate.

Figure 10: Hojiblanca Olive.

10) Gemlik

This type has medium vigor and spreading branches, and it ripens in

September-October. The fruit is medium (2.76 g), and it is used to

extract oil and table products. Fruit yields average is 25-30 kg per plant,

with a 15-16% extra virgin oil recovery rate.

Figure 11: Gemlik Olive.

11) Chemlali

This type has strong vigor and spreading cum drooping branches, and it

ripens in September-October. The fruit is small (0.32 g), and it is used

to extract oil and table use. Fruit yields average is 18-24-25 kg per plant,

with a 14-15% oil recovery rate.

Figure 12: Chemlali Olive.

12) Picual

This type has strong vigor and spreading cum drooping branches, and it

ripens in September-October. The fruit is small (0.32 g), and it is used

to extract oil and table use. Fruit yields average is 18-24 kg per plant,

with a 15% oil recovery rate.

Figure 13: Picual Olive.

### 2.2 OLIVE SELECTION FOR PROJECT

There is a wide range of olive plants in different parts of Pakistan. Olea Europaea, the biological name of olives, is locally known as zytoon in Urdu, shown in Pashto, Khat

in Brahvi, and known in Punjabi, Sindhi, and Saraiki.

Upon analyzing the various varieties of olives in Pakistan, it was concluded to opt for

two kinds of olives for utilization in the project: Ascolana and Arbequina. As both are

readily available and the environment of the region also favors their growth greatly.

### 2.3 EXISTING OLIVE PITTING MACHINE DESIGNS

Olives are used worldwide, so meeting the demand, olive devices are used worldwide.

Here are different types of olive pitting machines used. [6]

### 2.3.1 Machine Having Belt with Horizontal Punching:

This machine makes use of horizontal pins that are installed on conveyor belts.

When olives are placed on these beds, holders are responsible for clamping

them. Following this, the conveyor belts beneath the beds transfer the olives to

the pitting station of choice. The pitting station is equipped with a network of

horizontal needles for piercing olives and removing seeds. As the name

mentions, the destoning (seed removal) takes place due to the horizontal

positioning of the needles. This machine can pit up to 2000-2250 olive per

minute. The con of this machine is that it is costly, and costs up to $30000, is

huge and bulky. [7]

Figure 14: Machine having Belt with Horizontal Punching.

### 2.3.2 Machine Having Belt with Vertical Punching:

This machine is fundamental, and it consists of massive horizontal conveyor

belts. This machine has chambers with pockets where olives may be inserted.

This machine use a single pitting network with many needles to puncture the

olive machine Vision and retrieve the seed vertically. The range of this machine

is destoning 1500 olives per minute. So, this machine has less efficiency as

compared to a device with horizontal punching. The con of this machine is that

it is expensive and costs up to $25,000, and another disadvantage is that it lacks

in size ratio.

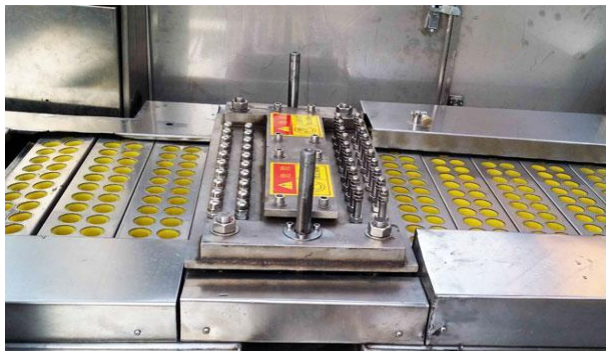
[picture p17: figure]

Figure 15: Machine having Belt with Vertical Punching.

### 2.3.3 Vertical Punching Machine with Circular Feed Plate:

As the name suggests, this machine consists of a circular feed plate on which

olives are placed. This machine uses the circular rotation principle, which says

that a circular plate rotates and sends the olives to pitting stations. This pitting

station also has several needles that pierce through the olive and remove seeds.

The con of this machine is that it is costly, up to $7000.

Figure 16: Mini Vertical Punching Machine with Circular Feed Plate.

### 2.4 SELECTED DESIGN FOR PITTING MACHINE

The Selected design of the machine resembles the cherry machine shown in figure 15,

with modification in the driving mechanism having a Geneva Mechanism Crank-Slider

Mechanism for the head of the device with a pitting needle. The machine is driven by

a 24 Volts DC-powered Motor, making it autonomous. Holes of Rollers are selected

according to the Grade of Olives needed to be pitted after being Graded by the Olive

Sorting Machine. The Pitting Machine Also includes Feeder and Collector Assembly

for Feeding and collecting olives, respectively [8].

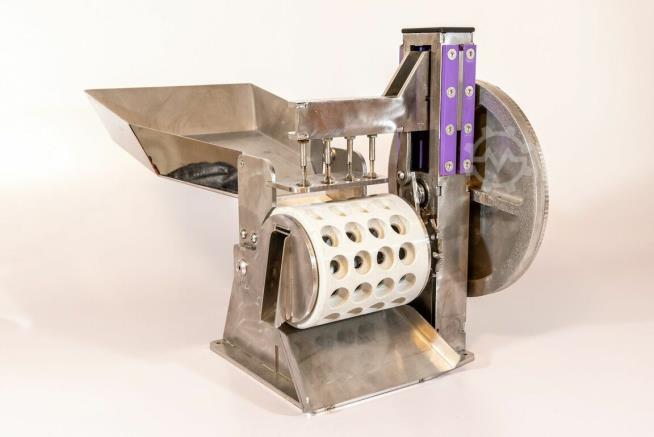
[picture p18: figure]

Figure 17: Cherry Pitting Machine. Design resemblance to the selected design of olive pitting

machine.

### 2.5 VARIOUS PARTS OF OLIVE PITTING MACHINE

Each Part of the Proposed Model is briefly explained below [9].

### 2.5.1 Olive Feeder:

The olive feeder is the essential and primary part of the olive pitting machine.

That’s why it is marked as the foundation and initial part of the machine. As the

name suggests, olives are deposited here. This part of the machine is manually

operated. The olive feeder is a container containing Graded Olives before

passing over to the pitting station. The olives in the feeder mustn’t get

overcrowded, so it is necessary to keep check and balance.

### 2.5.2 Olive Carrier:

Once the olives are successfully placed in the feeder, the next step is

successfully transferring olive to the pitting station so that it doesn’t get harmed.

This is done using a smooth mechanism to place olives in specific and desired

orientation for the pitting needles. If the olives are not placed in a particular

order, it may disfigure them, so for overcoming this issue, the carrier is in the

form of a roller drum. This roller consists of pockets responsible for holding

olives into their desired position so that the removal of seeds takes place

correctly. The roller drum is powered by a motor using a Geneva mechanism.

### 2.2.3 Pit Detaching Device:

It is an essential part of the machine as it removes seeds from the olives. This

device consists of multiple needles arranged and organized in a specific order

which are responsible for destoning. Another thing to note is that limiting or

fixing the number of needles is unnecessary. Still, the machine can use any

amount to remove seeds or stones depending upon the number of holes in the

carrier.

### 2.6 MECHANISMS USED IN OLIVE PITTING MACHINE

There are two types of mechanisms required for the machine. One is the slider-crank

mechanism (converts rotational motion to linear motion), and the other is the Geneva mechanism (exhibits intermittent motion). Both mechanisms are responsible for

transmitting the motor power to the pitting head of the machine and for the carrier.

### 2.6.1 Slider Crank Mechanism

It is a 4-bar link mechanism that has vast applications in automobiles and

actuators. It converts linear motion into rotational motion and vice versa. There

are two types of it named inline and offset. The requirement of a slider-crank

mechanism is completed using an offset slider-crank mechanism. Three

revolute joints are used in the slider-crank mechanism for converting linear to

rotational motion and vice versa. With the help of a compliant mechanism,

lubricant is less necessary, and maintenance issues are also solved [11].

Following are the significant components of the slider-crank mechanism:

1) Slider

It is used for linear motion over the surface. The distance between

ending points or extreme points are dictated by the radial rotation

distance of the crank.

2) Crank

The crank is responsible for rotational motion. The distance covered by

the slider between extreme points is always greater than twice the

crank radius.

3) Coupler

It is a connecting rod attached at one end with the crank and the other

with the slider. It converts the rotational motion of the crank into the

linear motion of the slider.

Figure 18: Crank Slider Mechanism.

### 2.6.2 Geneva Mechanism:

The Geneva mechanism is a cam like a mechanism that is used for intermittent

motion. Due to periodic motion, it holds importance as it is used in many

automatic machines. The reason for producing intermittent motion is due to the

configuration of its parts. Geneva mechanism has three types:

- Internal
- External
- Spherical

The best type is one having an external configuration. Following are significant

components of the Geneva mechanism.

1) Crank

It exhibits rotatory motion with the help of an external motor. The crank

rotates at uniform angular velocity and catches the slot of the Geneva

disc to exhibit intermittent motion. The crank moves one complete

rotation to exhibit periodic motion of Geneva Disc,

` | 2) Geneva Disc
| It is responsible for intermittent motion. The crank and slot of the

Geneva disc are mutually perpendicular to each other at the time of

engagement and disengagement. The periodic motion is dependent upon

the number of slots. The minimum number of slots required for the

Geneva disc is three, increasing up to 12 depending on the machine’s

complexity.

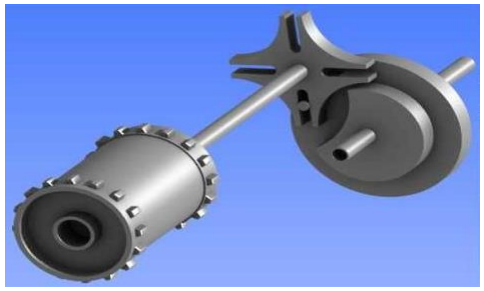
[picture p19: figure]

Figure 19: Geneva Mechanism.

### 2.7 SOME PREPROCESSING FOR OLIVES

Before putting olives for the removal of seeds or stones, it has to go through some

processes. These processes include checking the quality of olives to ensure no cavity

or moisture faces are there, Grading/Sorting of Olives. The olives that come into the

market have a high risk of other elements, such as stems, leaves, or other foreign

elements. So, to avoid any malfunctioning, these elements need to be removed

manually. The second method is specific for both black and green olives. These olives

need to be soaked into bine solution for almost 30-40 minutes so that the olives get

soft, and the needle can easily penetrate through it; otherwise, the needle can break or

cause malfunctioning in the machine.

### 2.8 GRADING/ SORTING OF OLIVES

Food Grading and Food Sorting may seem similar but have a primary difference in the

industry. Food Grading is a producer used to differentiate fruits/vegetables based on

more than one property: color, weight, cavity, processed or unprocessed. In sorting, food is distinguished based on only one property: color, weight, cavity, processed or

unprocessed.

Based on research, Food Grading/Sorting Include Two Basic Methodologies being

used in the industry. Machine Vision Driven Grading and Mechanical Based Grading.

Although The Machines may vary in design and material/electronic used, the primary

methodologies remain the same. Both Methodologies being considered for Olive

Sorting Machine are briefly explained below.

### 2.8.1 Food Grading by Machine Vision:

In this modern era of industrialization, machine vision has become the most

influential factor in revolutionizing the food industry. Food grading, including

the size, orientation, Volume, weight, color, and checking the quality of a

particular food type, has become very easy using computer vision. Machine

Learning and Machine Vision make the perfect artificial intelligence system

used for food processing. [10]

1) Working:

The most used Computer Vision Grading of Olives include grading by

Size and color. Modern image processing techniques are used to

distinguish the difference in color and sizes. For imaging, High-Speed

Cameras are used to capture images as fast as up to 120 frame rates.

Data Acquisition Card (DAC) is used to control the system. Machine

Learning is a must to process and compare the data to provide the best

results. For color identification, Machine Learning techniques are used

to easily differentiate between two colors that vary in intensities [11].

Figure 20: Olive Grading Machine Based on Machine Vision.

Figure 21: (a) Shows the machine’s interface (b) shows the high-speed cameras.

### 2.8.2 Mechanical System Based Olive Sorting:

Mechanical based system for olive grading is the most used methodology. This

system works based on conveyor belts and sorts the olives according to their

sizes which can be further sent for processing [10].

1) Working:

Mechanical Sorting Consists of Feeder Assembly through which olives

are sent to conveyor belts arranged so that they are hollow from the

bottom and carry the olives while moving forward. The carrier is

designed so that the initial distance between the two compartments is less and increasing as it moves forward. The olives fell according to

their size and are collected using a collector assembled below the belt

[10].

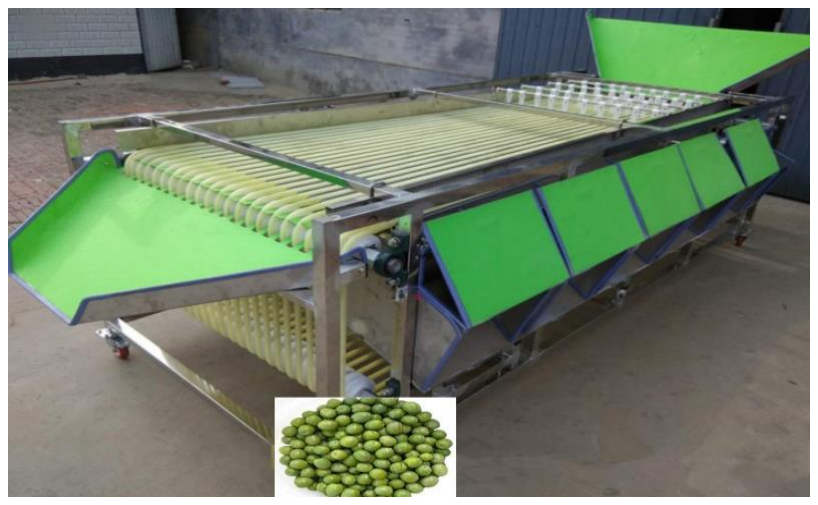
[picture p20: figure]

Figure 22: Shows the Mechanical Olive Sorting Machine Based on Sizes.

### 2.9 FOOD-GRADE MATERIALS

Fruit that passes through the pitting machine shouldn’t get corroded or change their

properties due to mixing up with elements or moisture present in the surrounding or on

the material. Food safe material ensures that there is no mixing up of hazardous

substances with the food. The FDA’s Food Rule also tells us the exact terminology of

preventing food from harmful substances and imparting taste, color, or smell. Such

materials are required to be

- Corrosion-resistant
- Safe
- Nonabsorbent and durable
- Manufactured in a sense that can easily be cleaned or washed.

It is the utmost duty of the manufacturer to keep strict supervision on these food

handling materials. They should be conscientious about choosing the food-graded

material.

Let takes an example that says that if a manufacturer or user takes a good quantity of

salt that contains chlorides and metal that is being used is reactive to chloride, then

corrosion occurs. So, manufacturer should keep a proper check and balance.

There are two most common types of Food Grade materials in Industry, metals and

plastics. But not all metals and plastics are food grade.

Also, a machine is only food-grade if there is no crack in any part of the machine and

is cleaned regularly to prevent any fungus from growing on it. Also is manufactured

using food-grade materials.

### 2.9.1 Food Grade Metals:

Here are some examples of food metals that can be used in the food industry

but with some limitations [12].

1) Cast iron:

Cast iron can be used for cooking purposes only on cooking surfaces

and in utensils for serving food. But for other purposes, cast iron cannot

be used as there are certain limitations to it. One important thing to

ponder is that iron without a protective layer would quickly react with

moisture and corrode.

2) Aluminum:

Aluminum is another food metal that is commonly used in the food

industry. Here are some advantages of it:

- Temperature tolerance
- Corrosion resistant
- Lightweight and low cost

However, despite having advantages, it also has some disadvantages. It

has low tensile strength and can easily be broken down.

3) Copper:

It is a metal used in the food industry for limited purposes as acids can

quickly attack it. Here are some of the limitation’s coppers were given

below:

- Not suitable for large-scale manufacturing.

- Copper and its alloys that have pH below six cannot be used in the

food industry, e.g., brass

4) Stainless steel:

Stainless steel comes in different varieties and types used in the food

industry. Given below are some of its types:

a) Fruit Grade 304 Stainless Steel:

They mostly used stainless steel is 304. It is mainly because of

its corrosion resistance.

Its surface is very easy to clean, and it can be electro polished to

a smooth and shiny surface. But excessive exposure to salts can

degrade the steel, and there are high chances of corrosion.

b) Fruit Grade 316 Stainless Steel:

This steel has a high percentage of nickel and chromium present

in it. It requires a very high temperature of more than (800

degrees centigrade or 1472 degrees Fahrenheit). The 316

stainless steel has the upper hand over 304 steels because it is

highly resistant to acids, alkalis, and chlorides.

c) Fruit Grade 430 Stainless Steel:

It is the primary stainless-steel type with the same chromium

percentage, but nickel concentration is different. It uses less

nickel percentage than 316. The 430 stainless steel is magnetic,

and it is resistant to stress corrosion cracking (the growth of

cracks that causes failure in the environment). It is also resistant

to many other elements, e.g., sulfur, nitric acids, organic acids.

One of its drawbacks is that the low percentage of nickel is not

immune to reducing acids.

CHAPTER 3: DESIGNING OLIVE PITTING MACHINE

### 3.1 DESIGN OF OLIVE PITTING MACHINE:

The design of olive pitting machine is not just based on olives characteristics but also

mechanism needed for machine. The material used for machine should have following

properties given below:

- Symmetric Geometry
- Uniform thickness
- Corrosion resistance
- Recyclability
- Strength and high endurance both at high and low temperature

So, the material we have selected for our machine which fulfills all required criteria is

stainless steel. The olives which we have chosen for our project are Arbequina and

Ascolona. We have chosen these types of olives as these are found in extensive parts

of Pakistan during harvesting season and hence suitable for our project.

Now we're talking about a system that will convey the olives from where they are on

the machine to where they will securely arrive in the container following the destoning

operation. The olives should not be damaged in this whole process otherwise it would

lose its commercial value.

### 3.2 COMPONENTS OF THE MACHINE:

Our machine design consists of six (6) components given below:

- Roller
- Stationary frame

- Needle box
- Geneva mechanism
- Olive feeder and olive collector
- Ac induction motor with inverter

### 3.2.1 Roller Drum:

The roller drum is the basic and fundamental component of machine used to

hold olives in predefined position. It has an advantage in a sense that it is

detachable and can be used for other types of olives. It consists of 8 lines of

pockets for holding olives and each at angle of 45 degree from one another. The

total pockets in roller drums are 72. The roller revolves along with needle box

for perfect destoning of olives. The roller is opened from one side and closed at

other side. The enclosed side is connected to Geneva mechanism for

intermittent motion of the roller. The size of each pocket is 12.5/15

(width/length). The width of roller drum is 60. 96cm.The 2D drawing of roller

drum is shown in figure below:

Figure 23: Drum Roller Assembly

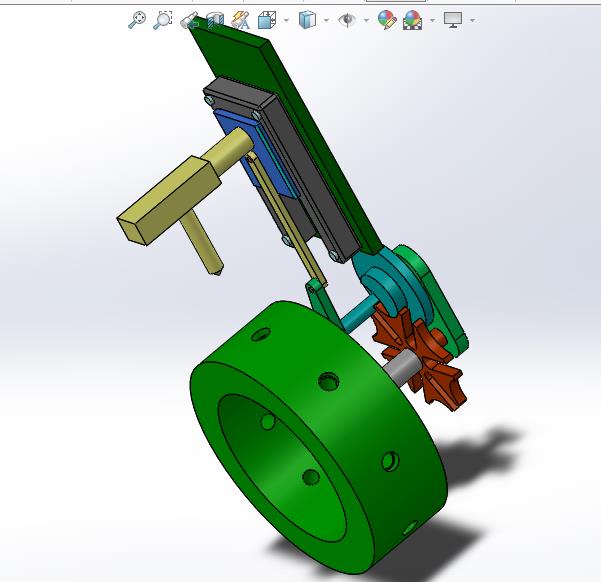
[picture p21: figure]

Figure 24: Baseless Assembly

### 3.2.2 Needle Box:

The function of the needle box is to remove the pit from olives. The needle box

consists of needles that will pierce through the olives and remove pit from it.

The needle box can also be customized just like roller drum. There are 9 needles

in the boxes one for each pocket. The needles are used to pierce into olives

present in the pockets at regular intervals. The width of needle is 7mm and

length is 20mm. The 2D drawing of needle is shown below:

Figure 25: Needle Box

### 3.2.3 Geneva mechanism:

The Geneva mechanism will provide an intermittent rotary motion to the

machine. It consists of following parts:

- Geneva driving wheel
- A locking plate with a pin
- Driven wheels with groves/slots

This mechanism also includes a connection that connects the roller box to the

needle. This connection is connected to the prime mover on one end and the

needle box on the other. Because the driven wheel contains 8 slots in this design,

the driver must revolve 8 times for each 45-degree rotation to accomplish 1

revolution. The pin drives the Geneva driving wheel at regular intervals,

supplying the necessary intermittent motion. The CAD model of Geneva disc

is shown below:

Figure 26: Geneva Mechanism

### 3.2.4 Olive feeder and Olive collector:

The trays that will hold the olives are the olive feeder and carrier. The machine

will begin with the olive feeder, and the placing of olives on the olive feeder

will be monitored by a human operator. The olive feeder will be inclined at 45 degrees to ensure a smooth movement of olives from feeder to drum. The CAD

model of olive feeder is shown below:

Figure 27: Olive Feeder

### 3.2.5 Seed Collector

Seed collector is used to collect the seeds after the olives have been successfully

pitted. It is placed inside the roller drum. The seed collector has 9 sockets

aligned with same number of sockets i.e., 9 with roller drum. The seeds of olives

are dropped in seed collector which provide non-mixing of olives flesh with its

seeds. The seeds can afterwards be used for extraction of olive oil or for various

purposes. The 3D model for seed collector is given below:

Figure 28: Seed Collector

### 3.2.6 AC induction motor:

For our project we have shortlisted some of motors such as DC stepper, AC

synchronous and AC induction motor. We have analyzed these three motors

and come to the point for using AC induction motor. It is a single-phase motor.

The motor has total power rating of 30 watts and 220 volts. The required ratio for functioning of the motor is 1:50.

### 3.2.7 Slider Crank Mechanism

Just like Geneva mechanism the cad model of slider crank mechanism is

divided into small several components which then assembled to form slider

crank mechanism. The first and most important component is crank. The crank

is responsible for rotational motion of mechanism that is converted into linear

motion. The crank is attached at one end with rotary motor and other end with

coupler. The 3D model is given below:

Figure 29: Crank

The next component which makes slider crank mechanism is slider. It is the

moving part and its exhibits linear motion. The distance moved by the slider

between its limiting points is always greater than twice the radius of the crank.

Coupler is used as joint to connect slider with the crank. The 3D model is given

below:

Figure 30: Coupler joined with crank

Coupler is responsible for converting rotary motion into linear motion. It

behaves like link which is attached at one end with slider and other end with

crank.

The base of the slider crank mechanism holds the structure upon which the

slider slides. The 3D model of base is given below:

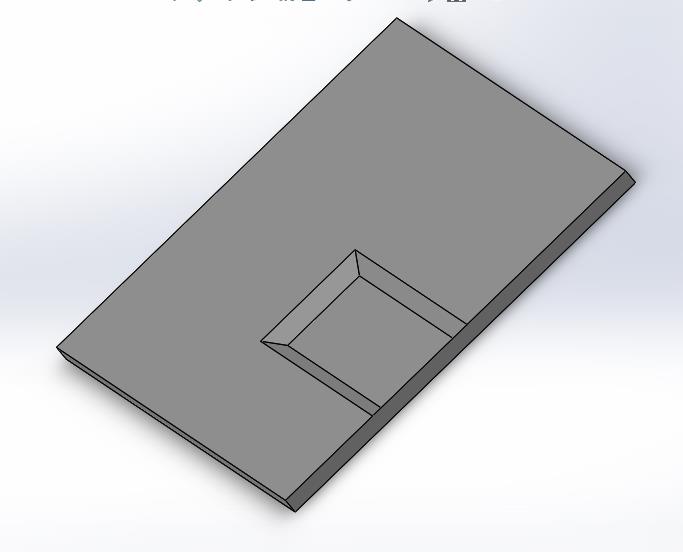
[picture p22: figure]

Figure 31: base of slider mechanism

The final assembly of slider crank mechanism obtained after making cad model of different

components and the assemble them together is given below

Figure 32: Slider Crank Mechanism

### 3.2.8 Figures of important parts of pitting mechanism:

Figure 33: Rod Atos

Figure 34: Structure

Figure 35: Pin

### 3.3 Complete assembly of Olive Pitting Extracting Machine:

After combining various mechanisms and components, the entire assembly of Olive Pit

Extractor machine is obtained. The shaft of the prime mover in the Geneva mechanism is

connected to the crank in the slider crank mechanism. The primary mover's wheel will be

turned by an AC induction motor. The crank would generate rotational motion, which would

be transformed into linear motion by the slider. The needle box is attached to the slider, and

when linear motion is produced, the needle box moves along with the slider to conduct pitting

operation. When the shaft of the prime mover catches on the slot of the driven wheel, it rotates

the roller drum 45 degrees and aligns the roller drum sockets with those of the needle box for

correct olive pitting. The complete assembly of olive pitting extraction machine is given below:

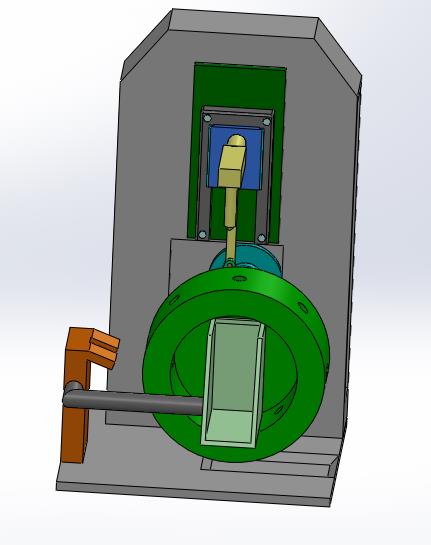
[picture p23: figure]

CHAPTER 4: DESIGN OF OLIVE GRADING MACHINE

Before moving onto practical implementation of machine it is necessary to conduct it

simulation as the priority to check whether there is shortcoming or not and then design it

practically. In this chapter we will discuss about designing of the olive grading machine i.e.,

Cad Cam model of machine and assembly of machine.

### 4.1 CAD MODELING:

Computer Aided Design has greatly accelerated the prototyping process. The creation

of the product is improved by visualizing it in 3D. Solid Model can be used for further

mechanical and functional analysis using different software.

The software we used for designing of machine is Solids Works 2018. It is such a

software developed by Dassault’s systems. This software is selected as this provide no

of functionalities. It is used for Cad Modelling of various parts of Olive Grading

Machine. Two designs of the machine were developed based on requirements. The first

design is capable of pitting 72 olives in one complete revolution of machine. The

second design is based on the first one and is for prototype.

Before cad modelling it is necessary to evaluate the dimensions of olives that will be

used in our machine as the roller drum and needle box will be customized keeping the

dimensions of olives in mind. As discussed earlier we have selected two types of olives

i.e., Arbequina and Ascolona. We have chosen arbequina for testing the prototype.

### 4.2 PROPOSED DESIGN:

After several set of calculations and iterations the complete design of olive pitting

machine is obtained. The design is capable of grading 100 olives in one complete

revolution of roller drum. Several components of machines are designed separately and

then assembled with pitting machine for the complete working mechanism. Following

are the important components of machine.

4.3 2D MODEL OF OLIVE GRADING MACHINE

The 2D model of the olive grading machine is designed on the Auto Cad. In the

following figures: the measurements of the different parts of grading machine are explained.

4.3.1 2D Design of Base Frame

Figure 37: Base Frame

Figure 38: Side View of Base Frame

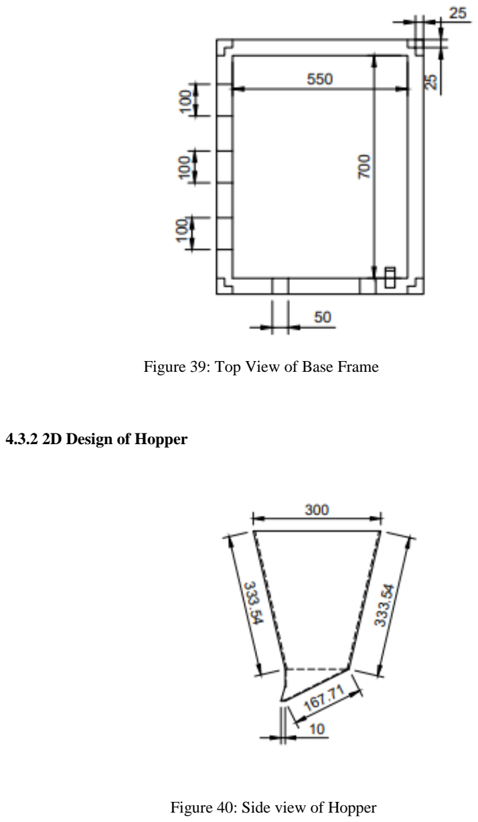
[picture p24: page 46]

Figure 39: Top View of Base Frame

4.3.2 2D Design of Hopper

Figure 40: Side view of Hopper

Figure 41: Top View

Figure 42: Side View of hopper

4.3.3 2D Design of holes on the roller drums

Figure 43: Diameter of Roller Drum Holes

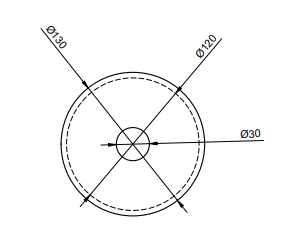
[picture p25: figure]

Figure 44: Front view of roller drum holes

4.3.4 2D Design of Roller Drums

Figure 45: Front view of roller drum

Figure 46: Side view of roller drum

Figure 47: Section View of rolling drums

4.4 3D CADMODEL DESIGN OF GRADING MACHINE

### 4.4.1 Flat Plate

1) Olives are delivered on this plate from the hopper. Width of the Flat plate is

140mm and the length is 304mm.

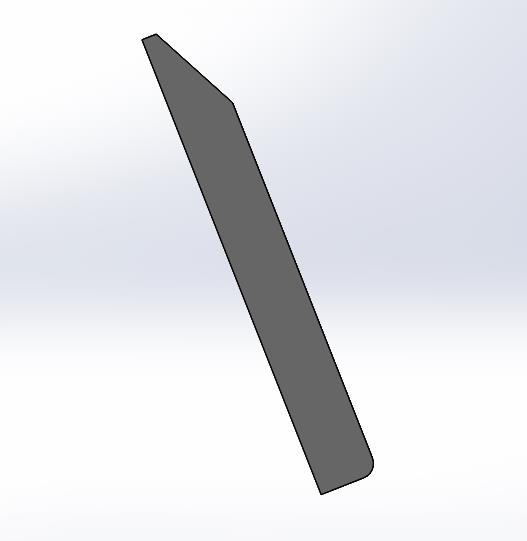
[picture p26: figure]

Figure 48: flat plate

### 4.4.2 Motor

220 volts AC supply motor is used to run the roller drums and the pulleys

attached to the machine.

Figure 49: Motor

### 4.4.3 Base

The length of the base frame is 330mm or 1.08 feet, width is 458mm or 1.5 feet.

The legs of the frame are 203mm or 0.66 feet.


Figure 50: Base

### 4.4.4 Rollers

1) Roller 1:

The length of the rolling drum is 1 feet or 305mm, 157 holes are present with

diameter 20 mm of each hole. The diameter of the drum is 92 mm or 3.6

inch.

Figure 51: Roller 1

2) Roller 2:

The length of the rolling drum is 1 feet or 305mm, 137 holes are present with

diameter 25 mm of each hole. The diameter of the drum is 92 mm or 3.6 inch.


Figure 52: Roller 2

3) Roller 3:

The length of the rolling drum is 1 feet or 305mm, 124 holes are present with

diameter 30 mm of each hole. The diameter of the drum is 92 mm or 3.6 inch.

Figure 53: Roller 3

### 4.4.5 Exit Plate:

Width of the exit plate is 140mm and the length is 295mm.

Figure 54: Exit Plate

### 4.4.6 Sprocket:

1) Sprocket

The teeth’s of the sprocket are engaged with the chain to move it through the

machine. Length of the shaft is 1 feet or 12 inches. Diameter of Sprocket is 2.25

inch or 57.15 mm.


Figure 55: Sprocket

### 4.4.7 Delivery Plate

Length of 1 compartment is 18 inch or 257 mm and its width is 5 inch or 127

mm.

Figure 56: Delivery Plate

### 4.4.8 Timing Belt and Chain

The teeth on the timing belt turn the camshaft in sync with the crankshaft.


Figure 57: Timing belt

### 4.5 FINAL 3D CADCAM MODEL

This is the final achieved 3D CAD model of olive grading mechanism, after

assembling all the parts discussed in chapter 4.

We entered the olives in 3 stages. First we put 5kg of olives then 10kg and in

3

rd stage we put 15kg of olives in the hopper, by 220 volts motor placed on the

other side of the machine, the rolling drums starts to roll. Respective olives fall

in 3 different categories according to their diameters which varies from 19mm

diameter to 29mm.

Figure 58: Final 3d Cad Model Of Gradig Machine

CHAPTER 5 - MATERIAL AND METHODS

### 5.1 FRUITS:

We will be discussing 2 types of olive crops in this study; “Ascolana and Arbequina”.

An approx. of 100 olives were used in our study. We collected the olive to be tested from the

farms in Barani Agriculture Research Institute, Chakwal. Then the measurements were taken

of the selected olives.

### 5.2 GRADING-MACHINE:

Following figures shows us the different parts being used in the grading machine,

schematic diagrams helps us to understand the parts of the grading machine. The parameters

depicted on the diagram are essentially those that will be determined for olives as a result of

this investigation, in order to alter the grading machine to perform efficiently with this fruit.

[12]

Figure 59: Top view of assembled machine


Figure 60: Side view of assembled machine

### 5.2.1 Designed Grading:

1) The Revolving Drums

Three revolving drums are made up of volcanized steel with following

parameters: Diameter 92mm, length 305 mm, spacing 6mm, thickness 4mm. The three

grading-drums have holes of diameters are 20, 25 and 30 mm number of holes are 156,

137 and 124.

Iron metal-sheet of 330mm length, 457 mm width and 1.5 mm (14 gauge) of

thickness was assembled above grading-drums spacing and bolted on two sides of fruit

boxes.

2) Fruit output unit

The output unit is made up of volcalnized steel with length of 457mm and width

of 127mm. Three fruit cutoffs were inserted into the three grading drums and fixed to

the left side of the frame. The fruits slide down the concave surface of the output unit

and fall into funnels. The curved section prevents fruits from being jammed. The

inclined angle of output unit calculated is 12 degrees.

### 5.2.2 Motor and Transmission System:

The grading system consists of 0.04 HP motor installed and chains are given

below:

Figure 61: Chains side view of assembled machine

### 5.3 DEVELOPMENT PHASES AND GRADING MACHINE COMPONENT

SPECIFICATIONS

The overall parameters of the olive hopper, grading drums with holes; the length and

diameters of drums, diameter and total number of holes and exit fall of the development

grading-machine are included as follows.

### 5.3.1 Olive hopper:

The top dimensions are of 350 x 330 mm and bottom dimensions of 350 x 80 mm. The frictional angle made with the hopper and 1st drum is 30 degree.

### 5.3.2 Grading Drums:

The fruits are graded into three sizes using revolving drums. The diameter of

the holes of the drum must be greater than the olives.

The fruit > 30 mm exit from the end of the machine. As there are 3 grading

drums for 3 different types of olives. Rotating/Grading drums and holes in it of varying diameter is 20mm. Length to accommodate 305 cm.

The tangential angle of the drums in the fruit output direction must be more

than 17 degree rolling angle between the olive fruits and the volcanized steel of grading

machine. The tangential angle of the drums at the direction of drum motion is 7 degrees.

### 5.3.3 Olive output unit

The tangential angle of the drums of rolling angles between the olives and

volcanized steel surface must be kept greater than 17 degree.

### 5.4 INSTRUMENTS INVOLVED IN THE PROCESS

### 5.4.1 Vernier Caliper

By the help of the Vernier Caliper with accuracy of 0.01mm we measured the

different dimension of the olives.

### 5.4.2 Digital balance

The accuracy of the digital balance is 0.2g it is used to measure the mass of the

olives.

### 5.4.3 Graduated cylinder

For calculation of the density and volume of the olives by immerging in water

of 1000ml with an accuracy of 25ml.

### 5.4.4 Friction and rolling-angle measuring device

An inclined plane was used to measure friction and rolling angles.

1) Friction angle measurement

The fruits are grouped together in a group on a horizontal surface, and the angle

of inclination is progressively increased until the fruits begin to slide without rolling.

Friction angles were calculated for each fruit group in a sample size of ten.

2) Rolling angle measurement

The fruits are placed one by one on flat plate, and the angle of elevation is

progressively raised until the olives start rolling. Two rolling angles are calculated for

each olive in an average sample (50).

### 5.5 Studied factors and measurements

The development grading-machine variables investigated were:

### 5.5.1 Grading speed:

Four different grading speeds 5, 8, 11 and 14 rpm (0.05, 0.08, 0.12 and 0.15 m/s).

### 5.5.2 Feeding rate:

Four different feed rates of 5, 10, 15 and 20 kg.

### 5.5.3 The Measurement were:

(1) Grading efficiency,
(2) Fruit damage
(3) Grading productivity.

### 5.6 Equations and Calculations

### 5.6.1 Sphericity Ratio

Sphericity ratio = fruit height (H) / fruit diameter (D) [13]

For olives: S.R = height / diameter

Table 1: Sphericity Ratio

Height (mm) | Diameter (mm) | Sphericity ratio
18.5 | 17.5 | 1.05
19.5 | 21.5 | 0.90
22.5 | 26.5 | 0.84

### 5.6.2 Projected Area

Projected area = 4/π (D * H)

Table 2: Projected Area

Height (mm) | Diameter (mm) | Projected area (mm²)
18.5 | 17.5 | 412.21
19.5 | 21.5 | 533.08
22.5 | 26.5 | 759.16

### 5.6.3 Real Density

Real density = Mass / Volume; Volume = 4/3 (3.14)(r³)

Table 3: Real Density

No. | Mass (kg) | Volume (mm³) | Real Density (kg/mm³)
1 | 5 | 2758.33 | 0.0022
| | 3882.42 | 0.0013
| | 5694.12 | 0.0009
2 | 10 | 2758.33 | 0.0036
| | 3882.42 | 0.0025
| | 5694.12 | 0.0018
3 | 15 | 2758.33 | 0.0054
| | 3882.42 | 0.0038
| | 5694.12 | 0.0026

### 5.6.4 Grading Productivity

According to; [14]

P = 3600 * M

T

P = Grading Productivity (kg/h)

M = Mass in sample (kg)

T = Time in seconds (s)

Table 4: Grading Productivity

Mass in sample (kg) | Time in seconds (s) | Grading Productivity (kg/h)
5 | 120 | 150
10 | 180 | 200
15 | 300 | 180

### 5.6.5 Grading Efficiency

According to [14], the grading efficiency of each outlet was computed as

follows.

µ1 = M₀₁1/Mi1

µ2 = M₀₂1/Mi1

µ3 = M₀₃1/Mi1

µ4 = M₀₄1/Mi1

Where;

µ1, µ2, µ3 and µ4: Grading efficiency of fruits for each outlet in the

machine, (%)

Mi1, Mi2, Mi3 and Mi4: Mass of each class inside olive hopper, (kg)

M₀₁, M₀₂, M₀₃ and M₀₄: Mass of olives for each outlet in the machine, (kg)

### 5.6.6 Total Grading Efficiency:

The total grading efficiency can be calculated by the following equation:

µ = (µ1+ µ2+ µ3+ µ4) / 4

### 5.6.7 Mechanical damage

Percentage of the mechanical damage was calculated by the following

formula:

D.F = Nd / Nt x 100

Where;

Nd0= No. of damaged olives

Nt0= Total olives

Table 5: Mechanical Damage

damaged olives | Total olives | D.F
25 | 100 | 25
28 | 80 | 35
35 | 75 | 46.67

### 5.7 Results and Discussions

### 5.7.1. Physical properties of olive fruits:

Dimensions, sphericity, mass, volume, actual density, and projected area of

olive fruits are shown in Table 1. These statistics were collected on 100 fruit

samples using the criteria established. [13]

### 5.7.2. Dimensions of fruit

If the sphericity is less than 0.9; if the sphericity is larger than 1.1, the fruit is

classified as oblong. Roundness is assumed for the remaining fruits with

intermediate index values [15]

The majority (85%) of olive in sample were round (sphericity 0.9 - 1.1), with

oblong olive fruits accounting for 15% of the sample (sphericity 1.1 - 1.4).

CHAPTER 6: SIMULATION ON ANSYS

In this chapter we will design software model of our project. To evaluate this design of machine

it has been simulated and analyzed on different software named as Solid works and Ansys.

Different set of analysis and constrained has been performed on machine.

### 6.1 ANSYS SIMULATIONS:

### 6.1.1 Static structural Analysis of Grading Machine:

Roller drum tis subjected to different simulations and the result shows that

design of base of grading machine so strong and robust. The Mild steel has

Young Modulus of 2.10 x 10^9 pascal, which is used in manufacturing of

needle. The poison ratio is 0.40 and mesh size is 20 mm .Following are the

analysis run on this mechanism to test its robustness.

ANSYS software is used to perform analysis on different parts of grading

machine. Force being applied on the bottom plate of the machine, pressure

being applied on the rolling drums after olives are placed for grading and fixed

supports of the machine, the figures are as below


Figure 62: Fixed Support

Figure 63: Force on the bottom plate

Figure 64: Pressure on Rolling Drums

### 6.1.2 Simulation by load of 50N:

1) Directional and total deformation on x-axis:

A deformation option that displays all of your model's deformation results in

three coordinates (X, Y, and Z). We can examine the deformation result of your physical model in this direction by entering a coordinate (X, Y, or Z) in

directional deformation.

The directional deformation in x axis is applied on the roller drums. 50N load

was applied. The results shows that the stress is high, but it doesn’t exceed

certain limit. The pictorial representation of the result is shown below:


Figure 65: Directional Deformation in X axis – 50N

+

Figure 66: Total Deformation – 50N


2) Von Mises Stress and elastic strain:

The drum is subjected to elastic strain and von misses stress are analyzed. 50N

loads were applied to the drum. The results prove that drum is within limit and

there are no chances that it will fracture. The following pictures shows the result

carried out:

Figure 67: Analysis of Von-Mises Stress - 50N

Figure 68: Analysis of Elastic Strain – 50N

### 6.1.3 Simulation by load of 75N:

1) Directional and total deformation on x-axis:

The directional deformation in x axis is applied on the roller drums. 75N load

was applied. The results shows that the stress is high, but it doesn’t exceed

certain limit. The pictorial representation of the result is shown below:

Figure 69: Directional Deformation in X axis - 75N


Figure 70: Total Deformation -75N

2) Von Mises Stress and elastic strain:

The drum is subjected to elastic strain and von misses stress are analyzed. 75N

loads were applied to the drum. The results prove that drum is within limit and

there are no chances that it will fracture. The following pictures shows the result

carried out:

Figure 71: Analysis of Von-Mises Stress – 75N

Figure 262: Equivalent Elastic Strain – 75N

### 6.1.4 Simulation by load of 100N:

1) Directional and total deformation on x-axis:

The directional deformation in x axis is applied on the roller drums. 100N load

was applied. The results shows that the stress is high, but it doesn’t exceed

certain limit. The pictorial representation of the result is shown below:


Figure 73: Total Deformation – 100N

Figure 7427: Direction Deformation in X axis – 100N

2) Von Mises Stress and elastic strain:

The drum is subjected to elastic strain and von misses stress are analyzed. 100N

loads were applied to the drum. The results prove that drum is within limit and

there are no chances that it will fracture. The following pictures shows the result

carried out:


Figure 7528: Analysis of Von-Mises Stress – 100N

Figure 7629: Equivalent Elastic Strain – 100N

### 6.1.4. Roller Drum Carriers of Olives:

Roller drums are used for converting rotary motion to linear motion of fruit

from the delivery plate. The coupler link was subjected to different simulations.

The material for coupler is stainless steel and with Young Modulus of

2.10x10^7 pa. The mesh size is 20mm and poison ratio is 0.40. Following are

analysis run on roller drums and complete structure of grading machine shows

its robustness.

### 6.2. Output of Machine:

The olive pitting and grading machine is simulated in SOLID WORKS for motion

analysis. The analysis shows that it is capable of grade 3 lines in 40 sec. We can

conclude that machine is capable of grade 40-50kg of olives under certain conditions

after analyzing the result.

Chapter 7: Conclusion and Future Work

Our grading machine established a mechanism for grading and pitting of olive fruits that has

vast applications as table salt and used for the extraction of olive’s oil. In addition to project

our senior degree we have designed a grading prototype machine for sorting of olives on their

sizes. The comparison of cost relative to other grading and pitting machines. The procedure

we have carried out shows that olive pitting and grading machine holds importance both

technically as well as from engineering point of view. The importance of this machine is

obvious from the fact provided that the production of such machines in Pakistan is

nonexistence due to lack of self-awareness and academic background. For pitting of olives, the

slider crank and Geneva mechanism is used but there are high chances of wear and tear of these

components so there are utmost requirements of some modifications in this design. Also, in

grading machine of olives there are also some errors carried out in making the holes of drum

roller for sorting of olives. Some holes are big enough that olives pass through it without going

through grading process. The research and academic work on this machine lacks in quality and

quantity of data needed for design of such machine.

The results we have carried out on this machine are given below:

The maximum fruit damage during pitting and grading process was 6.3 to 6.6%. This was

obtained with the grading speed of 8.2rpm (0.08 m/s) and feeding rate of 19kg. With the

grading speed of 11.1 rpm the minimum damage obtained was 3.2 to 3.4 % with the fruit size

of 20mm and feeding rate of 6kg. The maximum range of grading machine productivity for

olives of 112-835 was obtained with grading speed ranging from 6-15 rpm (0.06-0.16 m/s) and

feeding rate was 19kg. The minimum range of grading machine productivity for olives fruits

of 100-685 was obtained with grading speed of 5-14 rpm (0.06-0.15 m/s) and feeding rate of

5kg. The effective cost of our grading machine was from 38-40k.

Every machine has some error in it which arises due to certain conditions and factors, so our

machine has also some error in pitting of olives due to fruit damage as calculated earlier and

some holes of grading machine was not up to the mark for sorting of olives so in future, we

need to optimize this machine using different tools and techniques. The advancement in the

machine can made by converting it to fully automatic from semi-automatic machine. In this

way labor effort and cost is reduced and high efficiency can be obtained. This advancement in the machine can serve as economic booster in country as there is high demand of olive’s oil.

Another approach for future is data analysis techniques for machine and this can be carried out

by doing different calculations on the machine, making the table for different dimension for

parts of machine and performing mathematical calculations and doing different software

analysis using Ansys software. This improves the machine performance and efficiency. As this

is the continuous project from our senior degree which have worked on just pitting process and

we have done both pitting and grading processes. So, this is the advancement factor we have

made in our project by sorting olives on their sizes so that they can be utilized for olive oil

extraction or for food use. The grading machine we have made is semi-automatic that requires

motor for the start of roller drum. The motor starts by just plugging wire into switch. The drum

rotates and olives are fed to them the olives which are comparable to holes passes through it

and the ones which are bigger passes through next drum roller and there are collecting tray for

collecting of olives once they are graded.

## References

[1] F. J. Cimperman, "Machine for pitting and stuffing olives," [Online]. Available: https://patents.google.com/patent/US4388858A/en.
[2] T. Britannica, "Encyclopedia Britannia," Editors of Encyclopedia, 1 May 2019. [Online]. Available: https://www.britannica.com/plant/olive-plant. [Accessed 6 June 2022].
[3] Adda | Bjarnadottir, | "Healthline," | 21 | May | 2019. | [Online]. | Available:
healthline.com/nutrition/foods/olives. [Accessed 6 June 2022].
[4] PARC , "Pakistan Agriculture and Research council," 11 August 2014. [Online]. Available: http://www.parc.gov.pk/index.php/en/olive-history-of-olive-in-pakistan. [Accessed 6 June 2022].
[5] Tiwana; Zoha, "Paradigm Shift," 21 October 2021. [Online]. Available: https://www.paradigmshift.com.pk/olives-farming-in-pakistan/. [Accessed 5 June 2022].
[6] Barani Chakwal Institute Management, "Barani Agriculture Reseacrh Institute," 5 June 2013. [Online]. Available: barichakwal.punjab.gov.pk/background. [Accessed 4 June 2022].
[7] F. P. M. TYQH-06, "THOYU," 5 MAY 2015. [Online]. Available: thoyu.com/ty-qh06-fruit-pitting-machine.html. [Accessed 1 DEC 2021].
[8] M. M. C. Ltd, "Miracle Machinery," 2 Sep 2016. [Online]. Available: http://www.mrcfoodmachine.com/fruits-processing-machinery/olive-processing-machinery/automatic-olives-pitting-machine.html.
[9] SIA | Diapason, | "machineseeker," | 8 | Aug | 2016. | [Online]. | Available:
https://www.machineseeker.com/sia+diapason-m/i-5809770. | [Accessed | February
2022].
[10] E. G. M. G. H. J. U. S. Ahmed Faizan, "IEEE," June 2021. [Online]. Available: https://ieeexplore.ieee.org/abstract/document/9651337. [Accessed Jan 2021].
[11] T. | E. | o. | E. | Britannica, | "Britannica," | Britannica, | [Online]. | Available:
https://www.britannica.com/technology/slider-crank-mechanism.

[12] A. Lucas, "Deep learning in olive pitting machines by computer vision," 2018. [Online]. Available: sciencedirect.com/science/article/abs/pii/S0168169919310464. [Accessed 2022].
[13] IOSR-JAVS, "Journal of Agriculture and Veterinary Science," Agriculture and Veterinary Science, vol. 9, no. 11, pp. 2319-2380, 2016.
[14] TRENT BULLOCK, "WHAT DOES "FOOD GRADE" MEAN?," Dec 2017. [Online]. Available: https://www.csidesigns.com/blog/articles/what-is-food-grade.
[15] El-Raie, A.E.; M.M. Attaullah; K. S. Khalil, "Factors affecting the design of a grading machine for lemon fruits," Misr J. Ag. Eng., vol. 2, p. 29, 2012.
[16] Mohesenin, N. N.,, "Physical properties of plant and animal material," Gordon and Breach Sc. Pub., N. Y , vol. 734, 1986.
[17] Amin, E. E.,, "Development of a grading machine for some horticulture farm crops," J.Agric. Sci. Mansoura Univ, vol. 19(7), pp. 3139-3149, 1994.
[18] Buyanov, A. I.; Voronyuk, B. A., Physical and mechanical properties of plants, fertilizers and Soils, New Delhi, Bombay, Calcutta: Amerind Pub. Co., PVT, LTD, 1985.
[19] Awady, M. N.,, Engineering of tractors and agricultural machinery, Col. Ag., : Ain-shams Univ., 1998.
[20] M. M. Atallah, "DEVELOPMENT OF A GRADING MACHINE FOR OLIVES FRUITS," FARM MACHINERY AND POWER, vol. 29 , no. 2, pp. 569 - 590, April 2012.

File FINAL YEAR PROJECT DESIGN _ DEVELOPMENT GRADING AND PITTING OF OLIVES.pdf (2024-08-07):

DE-40 (MTS-A) S.M. SAIM NAVAID, M. OSAMA GUL, AHMED WAQAR RAO

DESIGN AND DEVELOPMENT OF OLIVE PITTING & GRADING MACHINE

COLLEGE OF
ELECTRICAL AND MECHANICAL ENGINEERING NATIONAL UNIVERSITY OF SCIENCES AND TECHNOLOGY RAWALPINDI 2022

DE-40 MTS-A; PROJECT REPORT; Mechatronics; Sponsoring DS:; Submitted By:; Dr. Hamid Jabbar; Syed M Saim Navaid; Dr. Umar Shahbaz Khan; Ahmed Waqar Rao

DESIGN AND DEVELOPMENT OF OLIVE

PITTING & GRADING MACHINE

Submitted to the Department of Mechatronics Engineering

In partial fulfillment of the requirements

For the degree of

Bachelor of Engineering

Muhammad Osama Gul

3

4

ACKNOWLEDGMENTS

We would like to thank our Supervisor, Dr. Hamid Jabbar and Co-Supervisor Dr. Umar Shahbaz

for his insight, guidance and help in accomplishing this task. It has been a privilege to work under

his supervision. We are grateful for his motivation and efforts that he gave us.

Furthermore we feel honored to have been taught by an excellent faculty and to have been graced

with peers and friends without whom my pursuit of education would have been less gratifying.

These acknowledgments would not be complete without expressing our appreciations for my family

whose continuous and firm support has enabled us to focus on our work without distraction.

We pray that Allah Almighty bestow upon them his blessings and bounties and continue to guide

us in our future endeavors.

THANK YOU.

ABSTRACT

The invention in the technological world in Olive processing industry which increases the

demand of the Olive industry. Olive pitting machine is mainly used for crushing and pitting of

olives. The destoning of olive is the major area of concern in this project. A prototype is

designed known as semi-autonomous machine for the extraction of olive and pitting process.

Our Project is mainly focus on the Design of the Olive pitting Machine & Grading Machine.

This machine will operate on no of mechanisms such as Geneva and slider crank mechanism.

The assembly of machine is designed keeping in mind that all sizes of olives can be placed in

one go on which pitting process need to be carried out. The major concern of our project lies

in passing olives through fruit grading machine and then after this put that passed Olive into

the Olive Pitting Machine whose task is to remove the seeds or pits of olives successfully the

without damaging the outer part of the fruit. The project we have chosen for our FYP has both

commercial and industrial value. The project holds to remove pit from olives mesh and then

these olives can serve application in foods we are used on daily basis like tables olives, pickled

olives and for extracting olives oil. Our area of target is to design a prototype whose

specifications is grading olive one their sizes and destoning of pits.

3

TABLE OF CONTENTS

ACKNOWLEDGMENTS | 4
ABSTRACT | 2
TABLE OF CONTENTS | 3
LIST OF TABLES | 7
CHAPTER 1: INTRODUCTION | 1
CHAPTER 2: LITERATURE REVIEW | 4
2.1.1 | Varieties of Olives in Pakistan | 5
2.2 | OLIVE SELECTION FOR PROJECT | 10
2.3 | EXISTING OLIVE PITTING MACHINE DESIGNS | 11
2.3.1 | Machine Having Belt with Horizontal Punching: | 11
2.3.2 | Machine Having Belt with Vertical Punching: | 12
2.3.3 | Vertical Punching Machine with Circular Feed Plate: | 12
2.4 | SELECTED DESIGN FOR PITTING MACHINE | 13
2.5 | VARIOUS PARTS OF OLIVE PITTING MACHINE | 14
2.5.1 | Olive Feeder: | 14
2.5.2 | Olive Carrier: | 14
2.2.3 | Pit Detaching Device: | 14
2.6 | MECHANISMS USED IN OLIVE PITTING MACHINE | 14
2.6.1 | Slider Crank Mechanism | 15
2.6.2 | Geneva Mechanism: | 16
2.7 | SOME PREPROCESSING FOR OLIVES | 17
2.8 | GRADING/ SORTING OF OLIVES | 17
2.8.1 | Food Grading by Machine Vision: | 18
2.8.2 | Mechanical System Based Olive Sorting: | 19
2.9 | FOOD-GRADE MATERIALS | 20
2.9.1 | Food Grade Metals: | 21
CHAPTER 3: DESIGNING OLIVE PITTING MACHINE | 23
3.1 DESIGN OF OLIVE PITTING MACHINE: | 23
3.2 COMPONENTS OF THE MACHINE: | 23
3.2.1 Roller Drum: | 24

4

5

5.3 DEVELOPMENT PHASES AND GRADING MACHINE COMPONENT

6

7

LIST OF TABLES

8

The final assembly of slider crank mechanism obtained after making cad model of different

9

CHAPTER 1: INTRODUCTION

Olives play significant role in dietary and for medical purposes all around the world. According

to a survey it is estimated that global olive market is projected to reach 17.2 billion dollars by

end of 2028. Pakistan has 10 million acres of land for olive production. Olive industry is

growing day by day with the in interventions of technological solutions in olives process

industry. The one of most important process is removal of pit from olives which is also our

required goal. There are two procedures for destoning of olives i.e.

- Partial destoning
- Total destoning

The project we have chosen for our FYP has both commercial and industrial value. The project

holds to remove pit from olives mesh and then these olives can serve application in foods like

tables olives and oil can also be extracted from the oils and is also used in pickels.

We are to design a semi automated machine whose function is to remove pit form olives. This

machine will operate on no of mechanisms such as Geneva and slider crank mechanism. All

size of olives can be placed in holes through which pitting needed to be performed [1]. There

are 3 major parts in this semi-automated machine i.e.

- Olive feeder
- Olive carrier
- Pit detaching device

Olive feeder is the only semi-automatic part of the machine. In olive feeder olives need to be

placed in such a way that it is in perfect contact with tip of needle and needle strike them

longitudinally.

Olive carrier is a revolving drum with sockets to hold various sizes of olives in predetermined

position. The 24V motor is needed to rotate this drum and when needle encounter olive means

when it strikes the olive then drum stop rotating. Usually, the sockets are designed in such way

2

to accommodate 72 olives at one instance. Mainly our goal is to cater destoning of two types

of olives i.e., Arbequina and Ascolana.

Pit detaching device consists of system of 9 needles which is capable of destoning 9 olives in

just one go. The device is based on phenomena known as Geneva Mechanism. The device is

designed in such a way that effective, and accuracy is obtained in destoning of olives. The one

thing is to keep in mind that needle should not damage the olives or itself while pitting process.

After destoning the olive’s flesh and seed is collected at different points. The invention in the

technological world in Olive processing industry which increases the demand of the Olive

industry. Olive pitting machine is mainly used for crushing and pitting of olives. Pit removal

is a major constraint in processing.

A semi-autonomous machine is designed for effective pit extraction. Our Project is mainly

focus on the Design of the Olive pitting Machine & Grading Machine. The major objective of

the of this project first to pass the olive through the Grading Machine and then after this put

that passed Olive into the Olive Pitting Machine which successfully remove the pit of the olives

without fracturing the outer part of the fruit.

The pitted Olive fruit can give us the income generating tool by making olive table oils, pickled

olive and sliced or chopped olives can be use on pizza etc. The Selected design of the Olive

Extracting Machine resembles the cherry machine with modification in the driving mechanism

having a Geneva Mechanism Crank-Slider Mechanism for the head of the device with a pitting

needle.

The machine is driven by a 24 Volts DC-powered Motor, making it autonomous. Holes of

Rollers are selected according to the Grade of Olives needed to be pitted after being graded by

the Olive Sorting Machine. The Pitting Machine Also includes Feeder and Collector Assembly

for Feeding and collecting olives, respectively.

Mechanical System Based Olive Sorting: Mechanical based system for olive grading is the

most used methodology. This system works based on conveyor belts and sorts the olives

according to their sizes which can be further sent for processing.

3

Mechanical Sorting Consists of Feeder Assembly through which olives are sent to conveyor

belts arranged so that they are hollow from the bottom and carry the olives while moving

forward. The carrier is designed so that the initial distance between the two compartments is

less and increasing as it moves forward. The olives fell according to their size and are collected

using a collector assembled below the belt.

Problems & Shortcomings in the Previous Design:

- No Testing of olives on Machine was performed because Season was over.
- No Grading Mechanism
- Pin Configuration
- Food Grade Material

A new Enhanced working Olive pitting Machine & Grading Machine will be delivered in our

project.

4

CHAPTER 2: LITERATURE REVIEW

Olives are found in central Tropical, Asia, and Mediterranean tropical and in different regions

of Africa. It has also become an emblem of Greek heritage in the modern world. The olive tree

is one of the most treasured and sacred trees among Greeks, and its significance is deeply

established in Greek mythology and history [1]. Olives are far too bitter to consume raw and

can only be relished after treatment, usually curing or pickling. Most olives are turned into

olive oil, although some are preserved and used in dishes, mainly Mediterranean cuisine.

Olives roughly provide about 115 to 145 calories per 100 grams or 59 calories per 10 olives.

Because of their high lipid content, olives are a unique fruit. Oleic acid is the most prevalent

fat in it, and it may offer various health benefits. They also contain 4–6% carbohydrates, the

majority of which is fiber. Vitamin E, iron, copper, and calcium are all abundant in olives. If

wrapped in saltwater, they could have much sodium in them [2].

Olives are high in antioxidants, which may help with many health benefits like lowering

cholesterol, which helps prevent heart diseases and blood pressure. They may also reduce your

cancer and bone loss risks [2]. Olives are used in the medicine and textile industry and for

manufacturing high-quality cooking oil for kitchen uses.

### 2.1 OLIVES IN PAKISTAN

Although Pakistan is not famous for its olive production, a wild subspecies of the olive

tree known as 'Olea cuspidate' grows in various parts. The environment in Pakistan is

ideal for developing olive trees since they grow quickly and thrive in the mild winters

that follow a long hot summer [3].

5

Figure 1: Existing olive plantation in Pakistan.

There are more than ten varieties of olives are being cultivated in different regions of

Pakistan. Both Soil and Environmental factors are very suitable for the large-scale

cultivation of olives in Pakistan, including the mountainous areas such as Balochistan.

The most favorable regions to olive cultivation include Killah Saifullah, Zhob,

Chakwal, Musakhali, Khuzdar, Potohar Regions, and the various areas of Balochistan

and KPK. [4]

### 2.1.1 Varieties of Olives in Pakistan

The Top 12 Varieties of olives in Pakistan include Koroneiki, Arbequina,

Pendolino, Jerboui, Earlik, Hamdi, Manzanilla, Ascolana, Hojiblanca, Gemlik,

Pecual, chemlali [5].

1) Koroneiki

This type has medium vigor and erect branches, and it ripens in October.

The fruit is small (0.93g) and is used to extract oil. Fruit yields average

18-22 kg per plant, with a 16.22% oil recovery rate.

6

Figure 2: Koroneki.Olives

2) Arbequina

This type has medium vigor and erect branches, and it ripens in October.

The fruit is small (1.87 g), and it is used to extract oil. Fruit yields

average is 20-25 kg per plant, with a 15-18% oil recovery rate.

Figure 3: Arbequina Olive.

3) Pendolino

This type has strong vigor and spreading branches, and it ripens in

September. The fruit is small (1.72 g), and it is used to extract oil. Fruit

yields average is 25-35 kg per plant, with a 20% oil recovery rate.

Figure 4: Pendolina Olive.


7

4) Earlik

This type has weak vigor and spreading branches, and it ripens in

October. The fruit is Large (3.45 g), and it is used to extract oil and table

use. Fruit yields average is 30-35 kg per plant, with a 16-17% oil

recovery rate.

Figure 5: Earlik Olive

5) Hamdi

This type has weak vigor and drooping branches, and it ripens in

September-October. The fruit is medium (3.67 g), and it is used for table

products. Fruit yields average is 25-30 kg per plant, with a 15-17% oil

recovery rate.

Figure 6: Hamdi Olive.


8

6) Manzanilla

This type has weak vigor and spreading branches, and it ripens in

September-October. The fruit is large (4.60 g), and it is used to extract

oil. Fruit yields average is 20-25 kg per plant, with a 15-17% oil

recovery rate.

Figure 7: Maznzanilla Olive.

7) Ascolana

This type has strong vigor and spreading cum erect branches, and it

ripens in October. The fruit is large (4.56 g), and it is used to extract oil

and table use. Fruit yields average is 20-25 kg per plant, with a 14-15%

oil recovery rate.

Figure 8: Ascolana Olive.

8) Jerboui

This type has medium vigor and spreading branches, and it ripens in

September. The fruit is medium (2.80 g), and it is used to extract oil.

Fruit yields average is 20-24 kg per plant, with a 20-21% oil recovery

rate.

9

Figure 9: Jerboui Olive.

9) Hojiblanca

This type has medium vigor and spreading branches, and it ripens in

September-October. The fruit is medium (4.1 g), and it is used to extract

oil and table use. Fruit yields average is 22-26 kg per plant, with a 16-

18% oil recovery rate.

Figure 10: Hojiblanca Olive.

10) Gemlik

This type has medium vigor and spreading branches, and it ripens in

September-October. The fruit is medium (2.76 g), and it is used to

extract oil and table products. Fruit yields average is 25-30 kg per plant,

with a 15-16% extra virgin oil recovery rate.

Figure 11: Gemlik Olive.

10

11) Chemlali

This type has strong vigor and spreading cum drooping branches, and it

ripens in September-October. The fruit is small (0.32 g), and it is used

to extract oil and table use. Fruit yields average is 18-24-25 kg per plant,

with a 14-15% oil recovery rate.

Figure 12: Chemlali Olive.

12) Picual

This type has strong vigor and spreading cum drooping branches, and it

ripens in September-October. The fruit is small (0.32 g), and it is used

to extract oil and table use. Fruit yields average is 18-24 kg per plant,

with a 15% oil recovery rate.

Figure 13: Picual Olive.

### 2.2 OLIVE SELECTION FOR PROJECT

There is a wide range of olive plants in different parts of Pakistan. Olea Europaea, the

11

biological name of olives, is locally known as zytoon in Urdu, shown in Pashto, Khat

in Brahvi, and known in Punjabi, Sindhi, and Saraiki.

Upon analyzing the various varieties of olives in Pakistan, it was concluded to opt for

two kinds of olives for utilization in the project: Ascolana and Arbequina. As both are

readily available and the environment of the region also favors their growth greatly.

### 2.3 EXISTING OLIVE PITTING MACHINE DESIGNS

Olives are used worldwide, so meeting the demand, olive devices are used worldwide.

Here are different types of olive pitting machines used. [6]

### 2.3.1 Machine Having Belt with Horizontal Punching:

This machine makes use of horizontal pins that are installed on conveyor belts.

When olives are placed on these beds, holders are responsible for clamping

them. Following this, the conveyor belts beneath the beds transfer the olives to

the pitting station of choice. The pitting station is equipped with a network of

horizontal needles for piercing olives and removing seeds. As the name

mentions, the destoning (seed removal) takes place due to the horizontal

positioning of the needles. This machine can pit up to 2000-2250 olive per

minute. The con of this machine is that it is costly, and costs up to $30000, is

huge and bulky. [7]

Figure 14: Machine having Belt with Horizontal Punching.


12

### 2.3.2 Machine Having Belt with Vertical Punching:

This machine is fundamental, and it consists of massive horizontal conveyor

belts. This machine has chambers with pockets where olives may be inserted.

This machine use a single pitting network with many needles to puncture the

olive machine Vision and retrieve the seed vertically. The range of this machine

is destoning 1500 olives per minute. So, this machine has less efficiency as

compared to a device with horizontal punching. The con of this machine is that

it is expensive and costs up to $25,000, and another disadvantage is that it lacks

in size ratio.

Figure 15: Machine having Belt with Vertical Punching.

### 2.3.3 Vertical Punching Machine with Circular Feed Plate:

As the name suggests, this machine consists of a circular feed plate on which

olives are placed. This machine uses the circular rotation principle, which says

that a circular plate rotates and sends the olives to pitting stations. This pitting

station also has several needles that pierce through the olive and remove seeds.

The con of this machine is that it is costly, up to $7000.

13

Figure 16: Mini Vertical Punching Machine with Circular Feed Plate.
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

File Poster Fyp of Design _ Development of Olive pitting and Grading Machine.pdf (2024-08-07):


Scanned with CamScanner

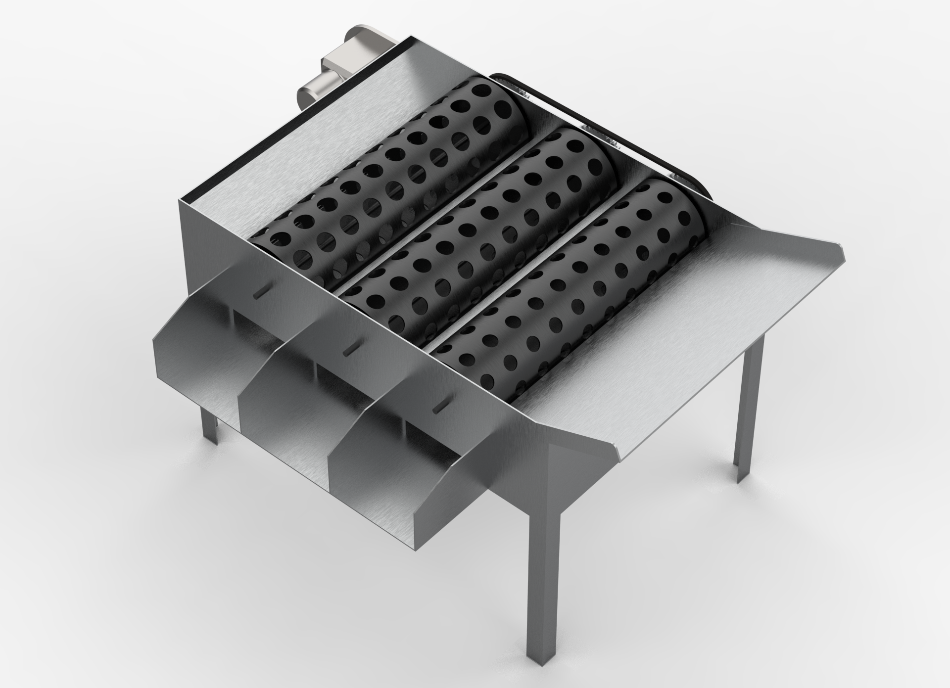
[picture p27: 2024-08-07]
Render 4 final design.png

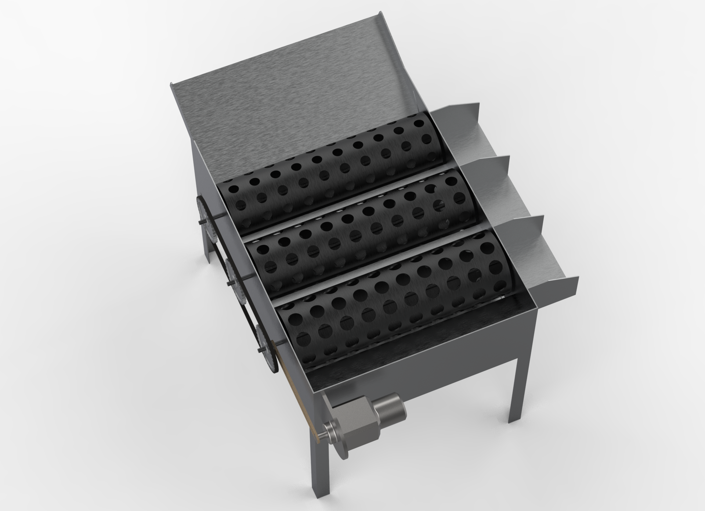
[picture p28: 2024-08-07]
Render 3 final design.png

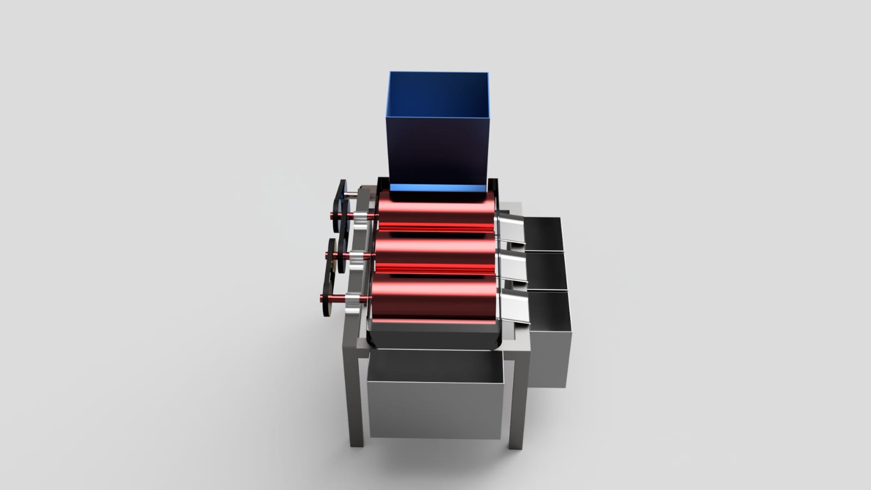
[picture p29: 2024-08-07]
Render 4 Ist Iteration.jpeg

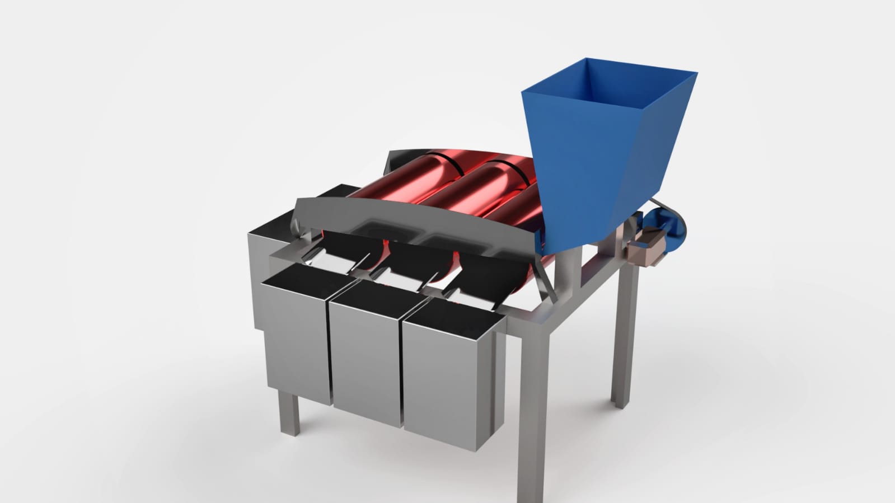
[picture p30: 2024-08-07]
Render Ist Iteration.jpeg

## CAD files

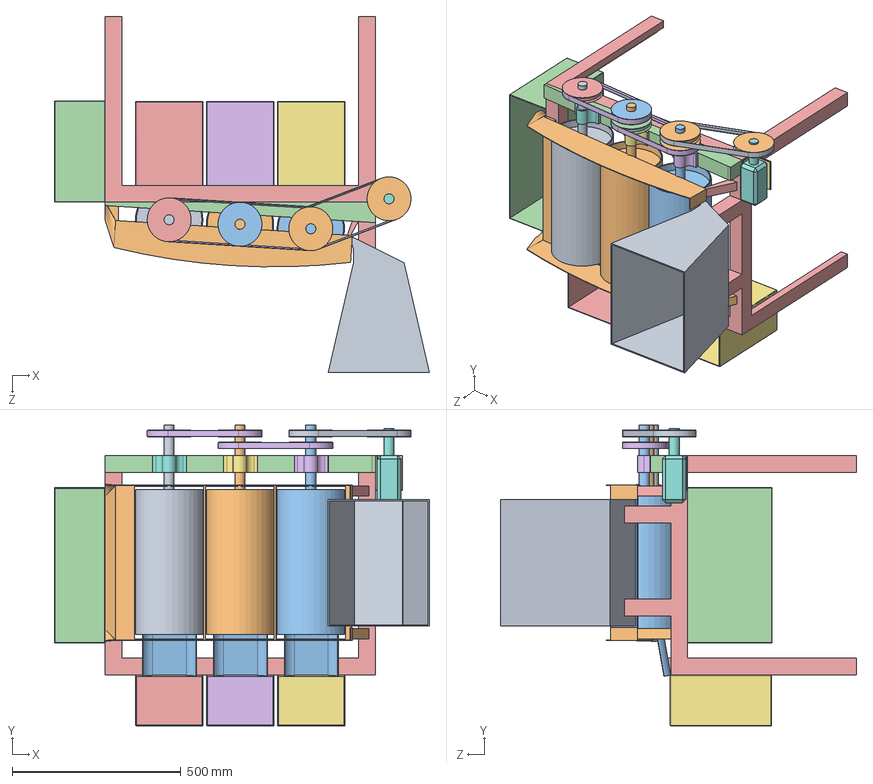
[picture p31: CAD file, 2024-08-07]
Grading_Machine.SLDASM
1109.7 x 890.3 x 1054.5 mm
Roller.step
Roller2.step
Roller3.step
Wedge.step
Base_Frame.step
Bearing3.step
Bearing2.step
Bearing1.step
Main_Container.step
Pulley1.step x 3
Pulley2.step
Pulley3.step
Pulley4.step
Belt.step x 2
Motor_Bracket.step
Motor.step
Drive_Belt.step
Tray.step
Slider.step x 3
Box1.step
Box2.step
Box3.step
Box4.step

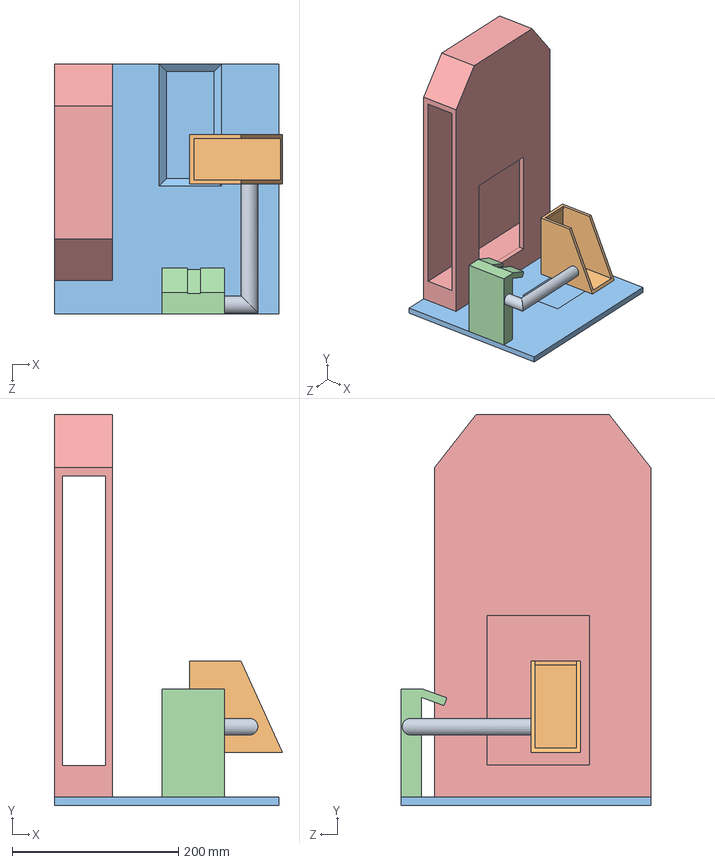
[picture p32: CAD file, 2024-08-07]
FYP Base of Assembly.SLDASM
274.1 x 470.0 x 300.0 mm
FYP Rod of Atos
FYP Seed Collector
FYP Bases of the base
FYP Olive Provider new
FYP Structure

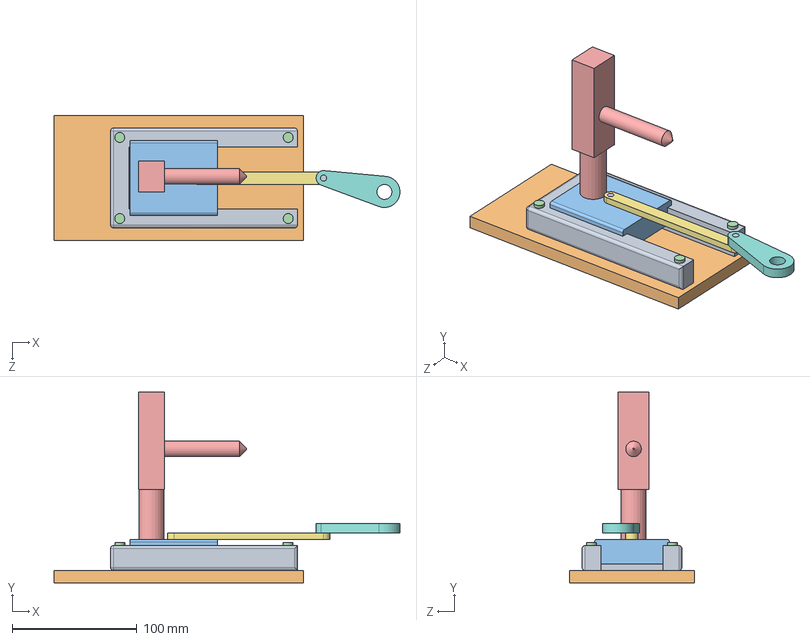
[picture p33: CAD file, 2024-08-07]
FYP Slider Crank Mechanism.SLDASM
277.3 x 153.0 x 100.0 mm
FYP Slider
FYP Basic
FYP Moving Part
FYP Bolt x 4
FYP Needle Box new(1)
FYP Pin1
FYP Link
FYP Crank
FYP Pin

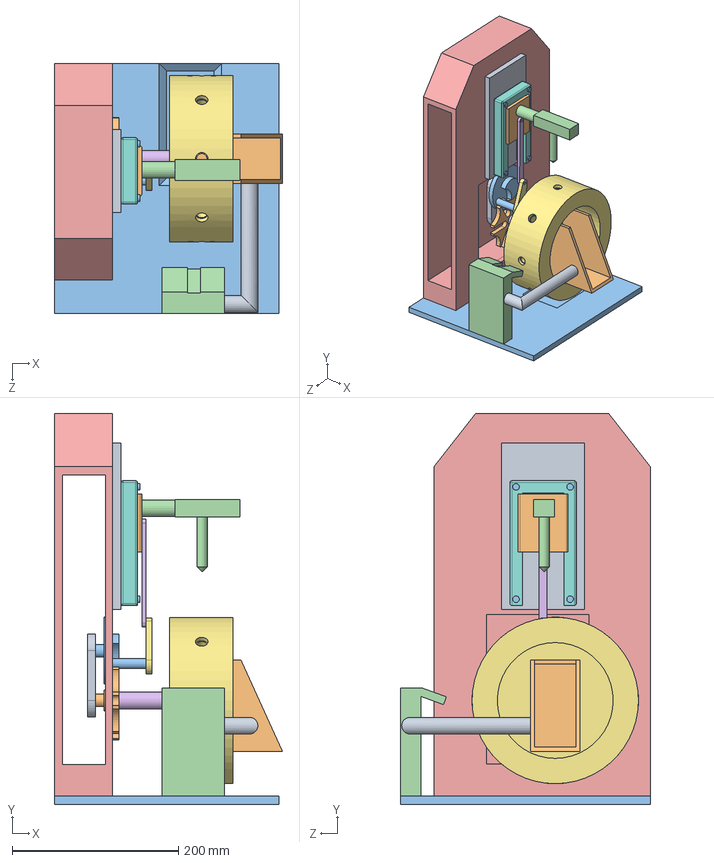
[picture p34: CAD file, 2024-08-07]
FYP Completed Assembly.SLDASM
274.1 x 470.0 x 300.0 mm
FYP Rod of Atos
FYP Seed Collector
FYP Bases of the base
FYP Olive Provider new
FYP Structure
FYP Drum Roller Support
FYP Drum Roller
FYP Slider
FYP Basic
FYP Moving Part
FYP Bolt x 4
FYP Needle Box new(1)
FYP Pin1
FYP Link
FYP Crank
FYP Pin
FYP Base
FYP Geneva Disc
FYP Prime Mover

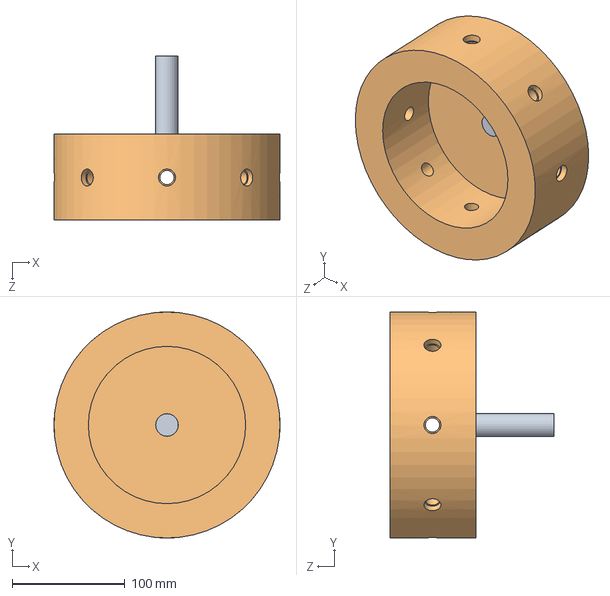
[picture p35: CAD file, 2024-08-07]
FYP Drum Roller Assembly.SLDASM
200.0 x 200.0 x 145.0 mm
FYP Drum Roller Support
FYP Drum Roller

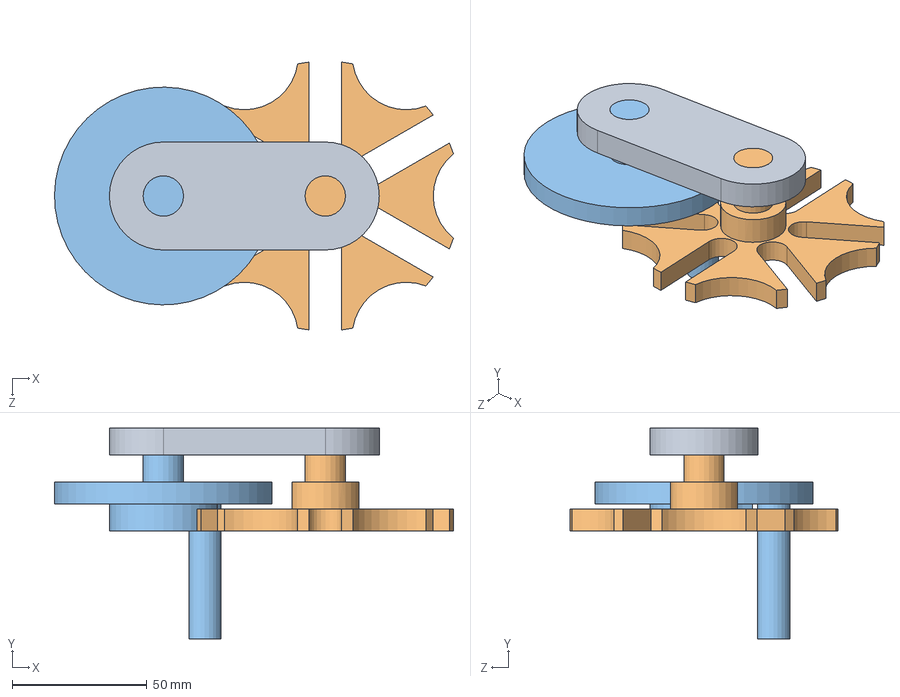
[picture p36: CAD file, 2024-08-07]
FYP Geneva Mechanism.SLDASM
147.8 x 78.0 x 99.3 mm
FYP Base
FYP Geneva Disc
FYP Prime Mover

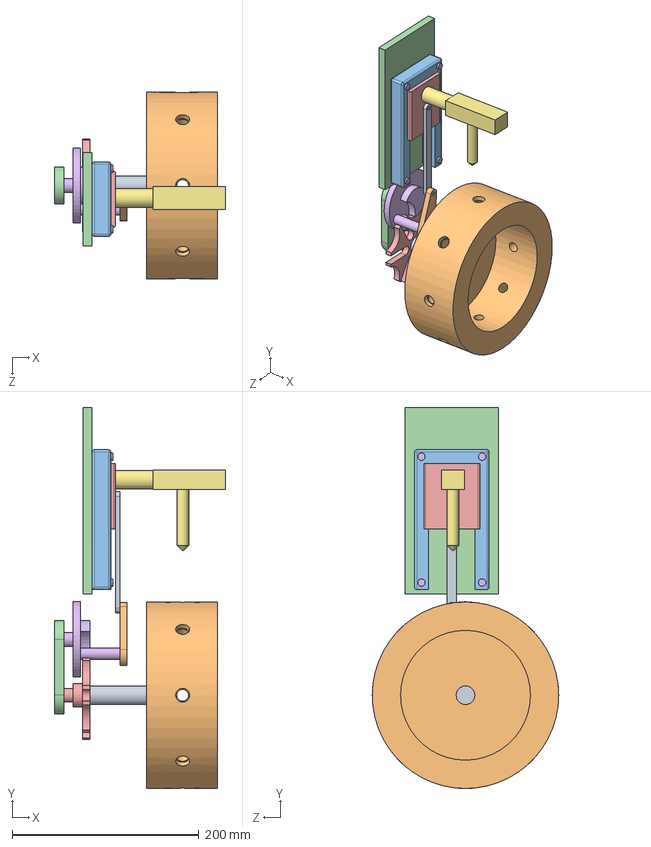
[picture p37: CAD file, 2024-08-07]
FYP Baseless Assembly.SLDASM
183.5 x 408.6 x 200.0 mm
FYP Drum Roller Support
FYP Drum Roller
FYP Slider
FYP Basic
FYP Moving Part
FYP Bolt x 4
FYP Needle Box new(1)
FYP Pin1
FYP Link
FYP Crank
FYP Pin
FYP Base
FYP Geneva Disc
FYP Prime Mover

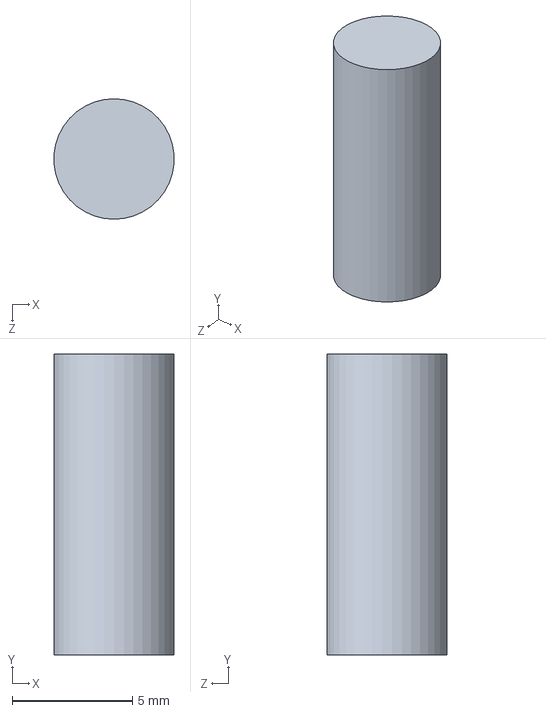
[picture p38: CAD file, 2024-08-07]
FYP Pin.SLDPRT
4.98 x 12.5 x 5.00 mm

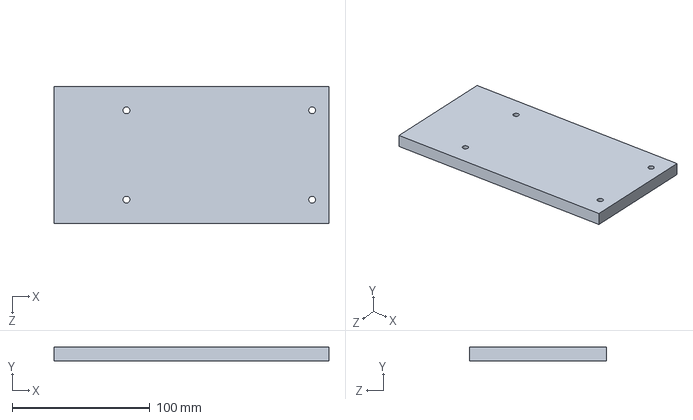
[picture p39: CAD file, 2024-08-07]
FYP Basic.SLDPRT
200.0 x 10.0 x 100.0 mm

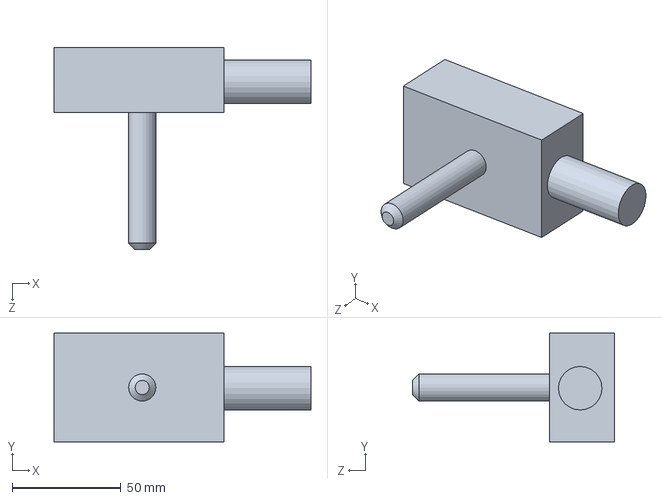
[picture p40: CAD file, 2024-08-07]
FYP Needle Box.SLDPRT
118.0 x 50.0 x 93.0 mm

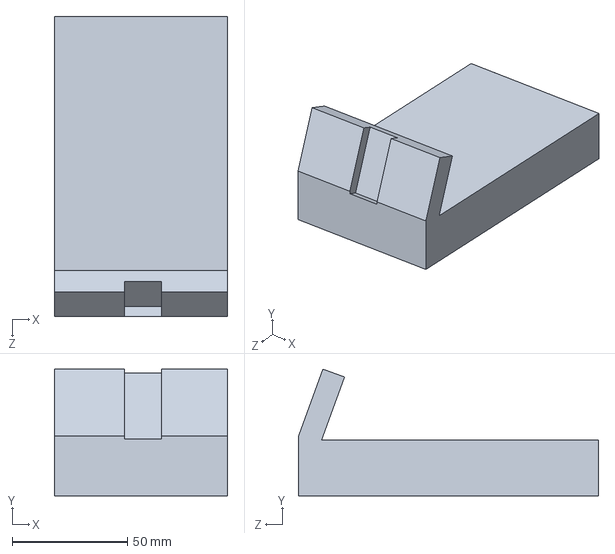
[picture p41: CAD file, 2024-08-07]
FYP Olive Provider.SLDPRT
75.0 x 54.9 x 130.0 mm

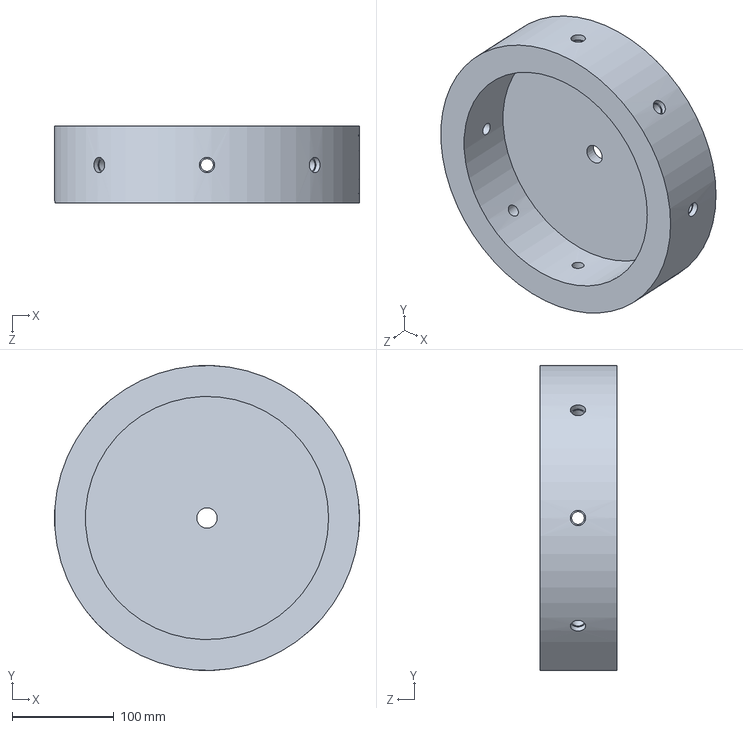
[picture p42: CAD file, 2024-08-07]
FYP Drum Roller30.SLDPRT
300.0 x 300.0 x 76.0 mm

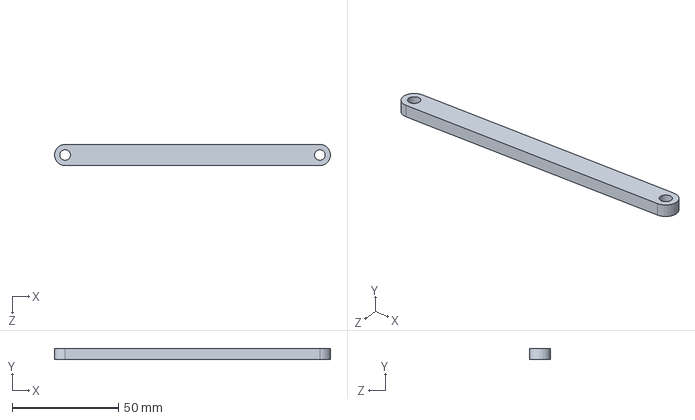
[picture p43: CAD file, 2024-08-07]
FYP Link.SLDPRT
130.0 x 5.00 x 10.0 mm

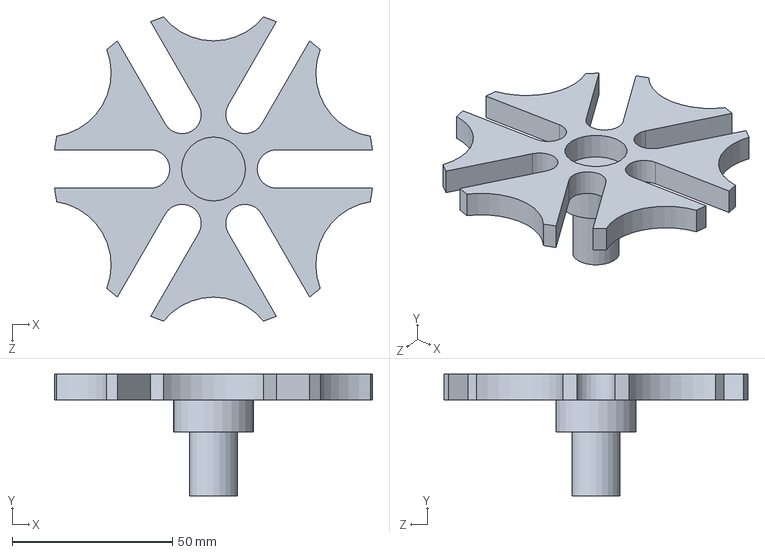
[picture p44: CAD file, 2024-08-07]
FYP Geneva Disc.SLDPRT
99.3 x 38.0 x 95.0 mm

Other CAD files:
FYP Base.SLDPRT
FYP Slider.SLDPRT
FYP Needle Box new(1).SLDPRT
FYP Pin1.SLDPRT
FYP Bases of the base.SLDPRT
FYP Bolt.SLDPRT
FYP Crank.SLDPRT
FYP Drum Roller Support.SLDPRT
FYP Drum Roller.SLDPRT
FYP Drum Roller25.SLDPRT
FYP Moving Part.SLDPRT
FYP Olive Provider new.SLDPRT
FYP Prime Mover.SLDPRT
FYP Rod of Atos.SLDPRT
FYP Seed Collector.SLDPRT
FYP Structure.SLDPRT

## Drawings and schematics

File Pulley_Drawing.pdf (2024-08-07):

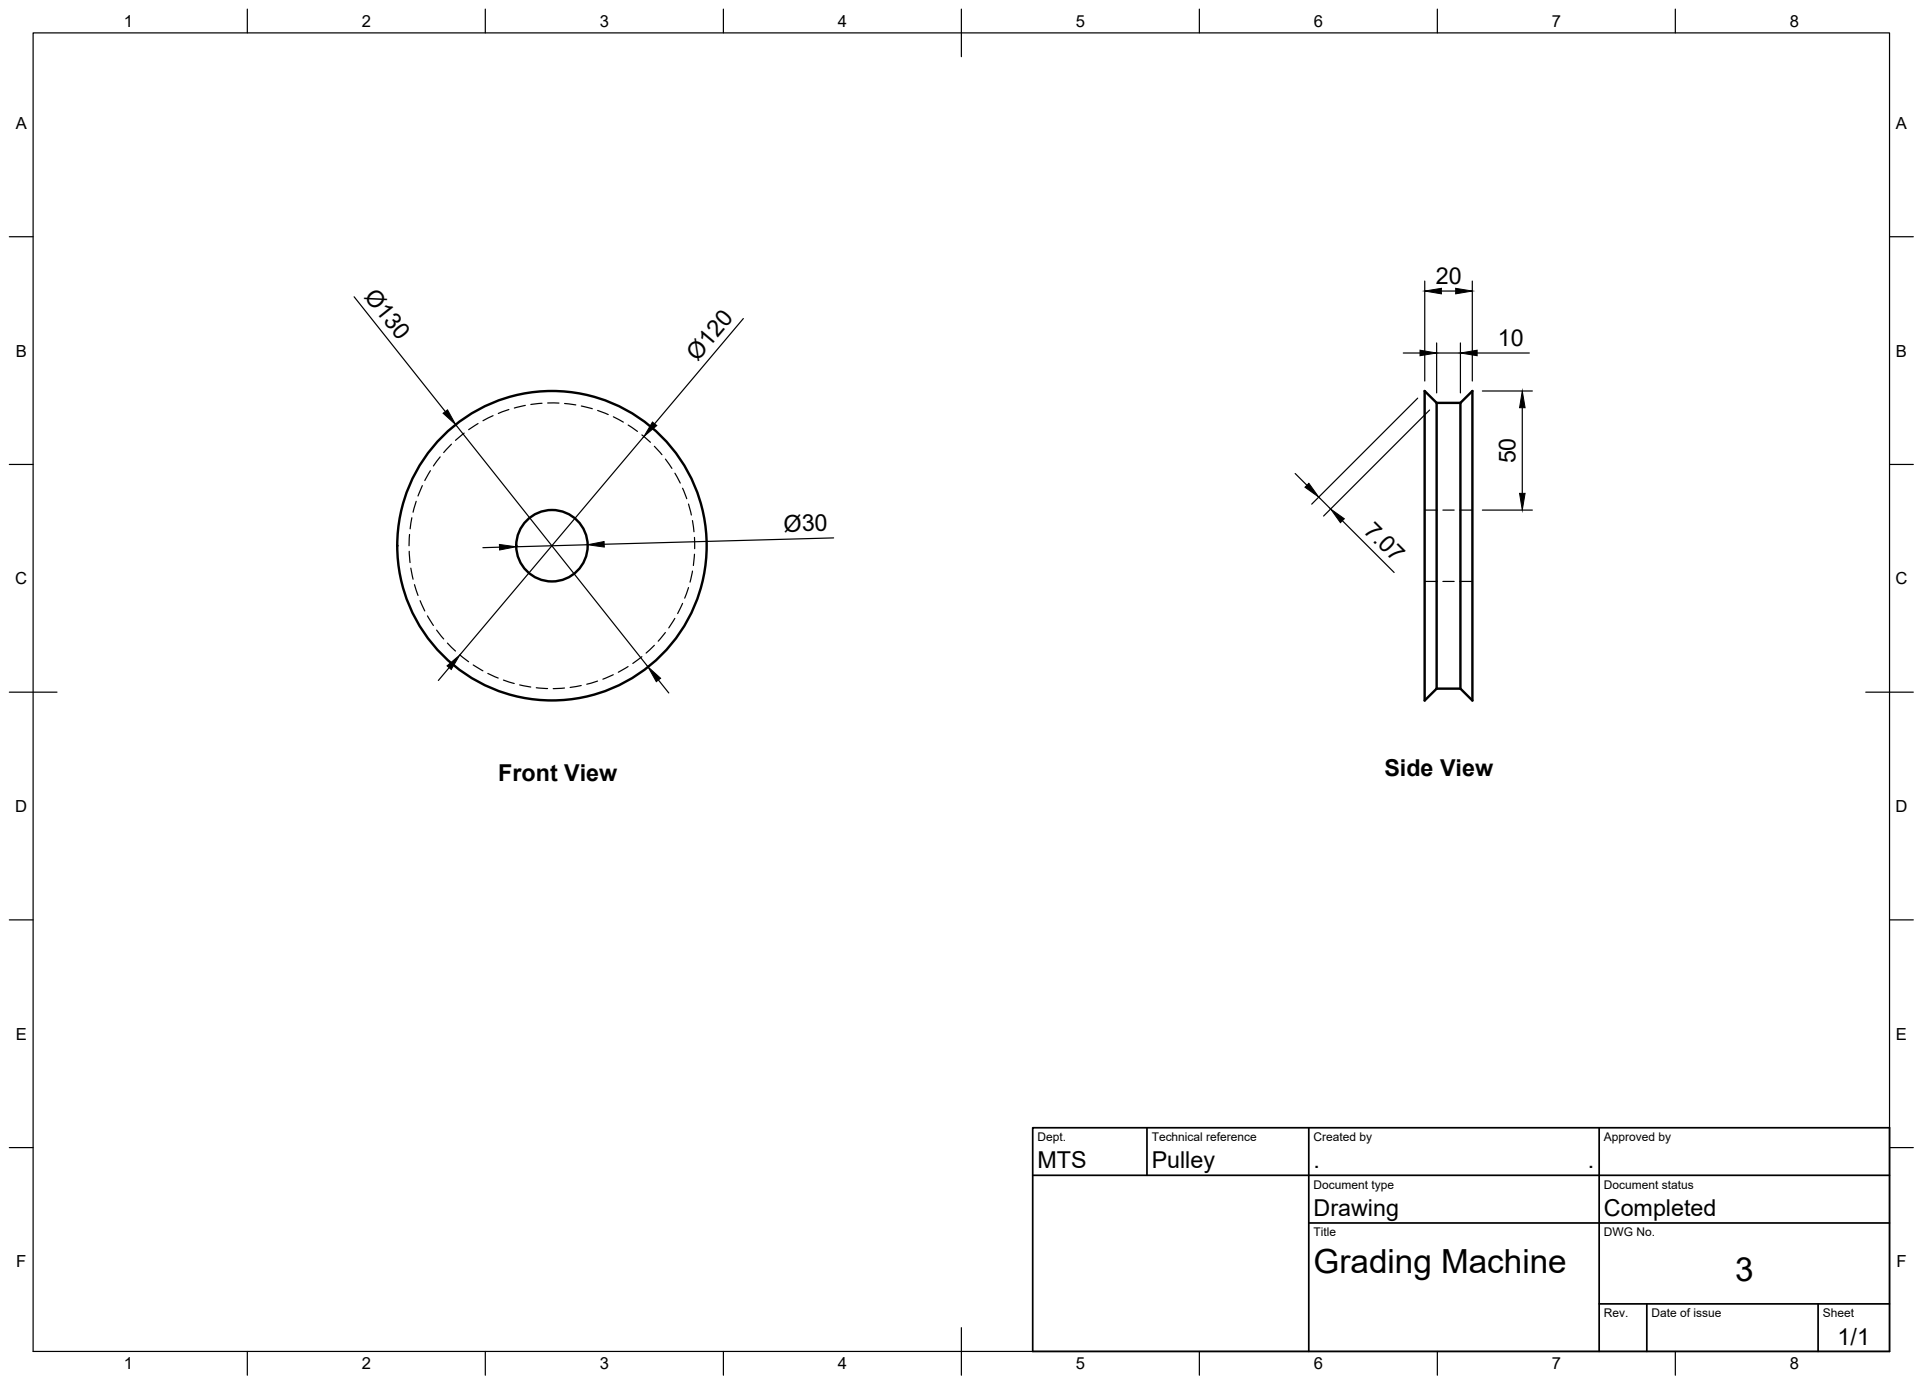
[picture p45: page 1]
Title; DWG No.; Rev.; Date of issue; Sheet; Grading Machine; Front View; Side View

Dept. MTS | Technical reference Pulley | Created by . . | Approved by

Document type Drawing | Document status Completed

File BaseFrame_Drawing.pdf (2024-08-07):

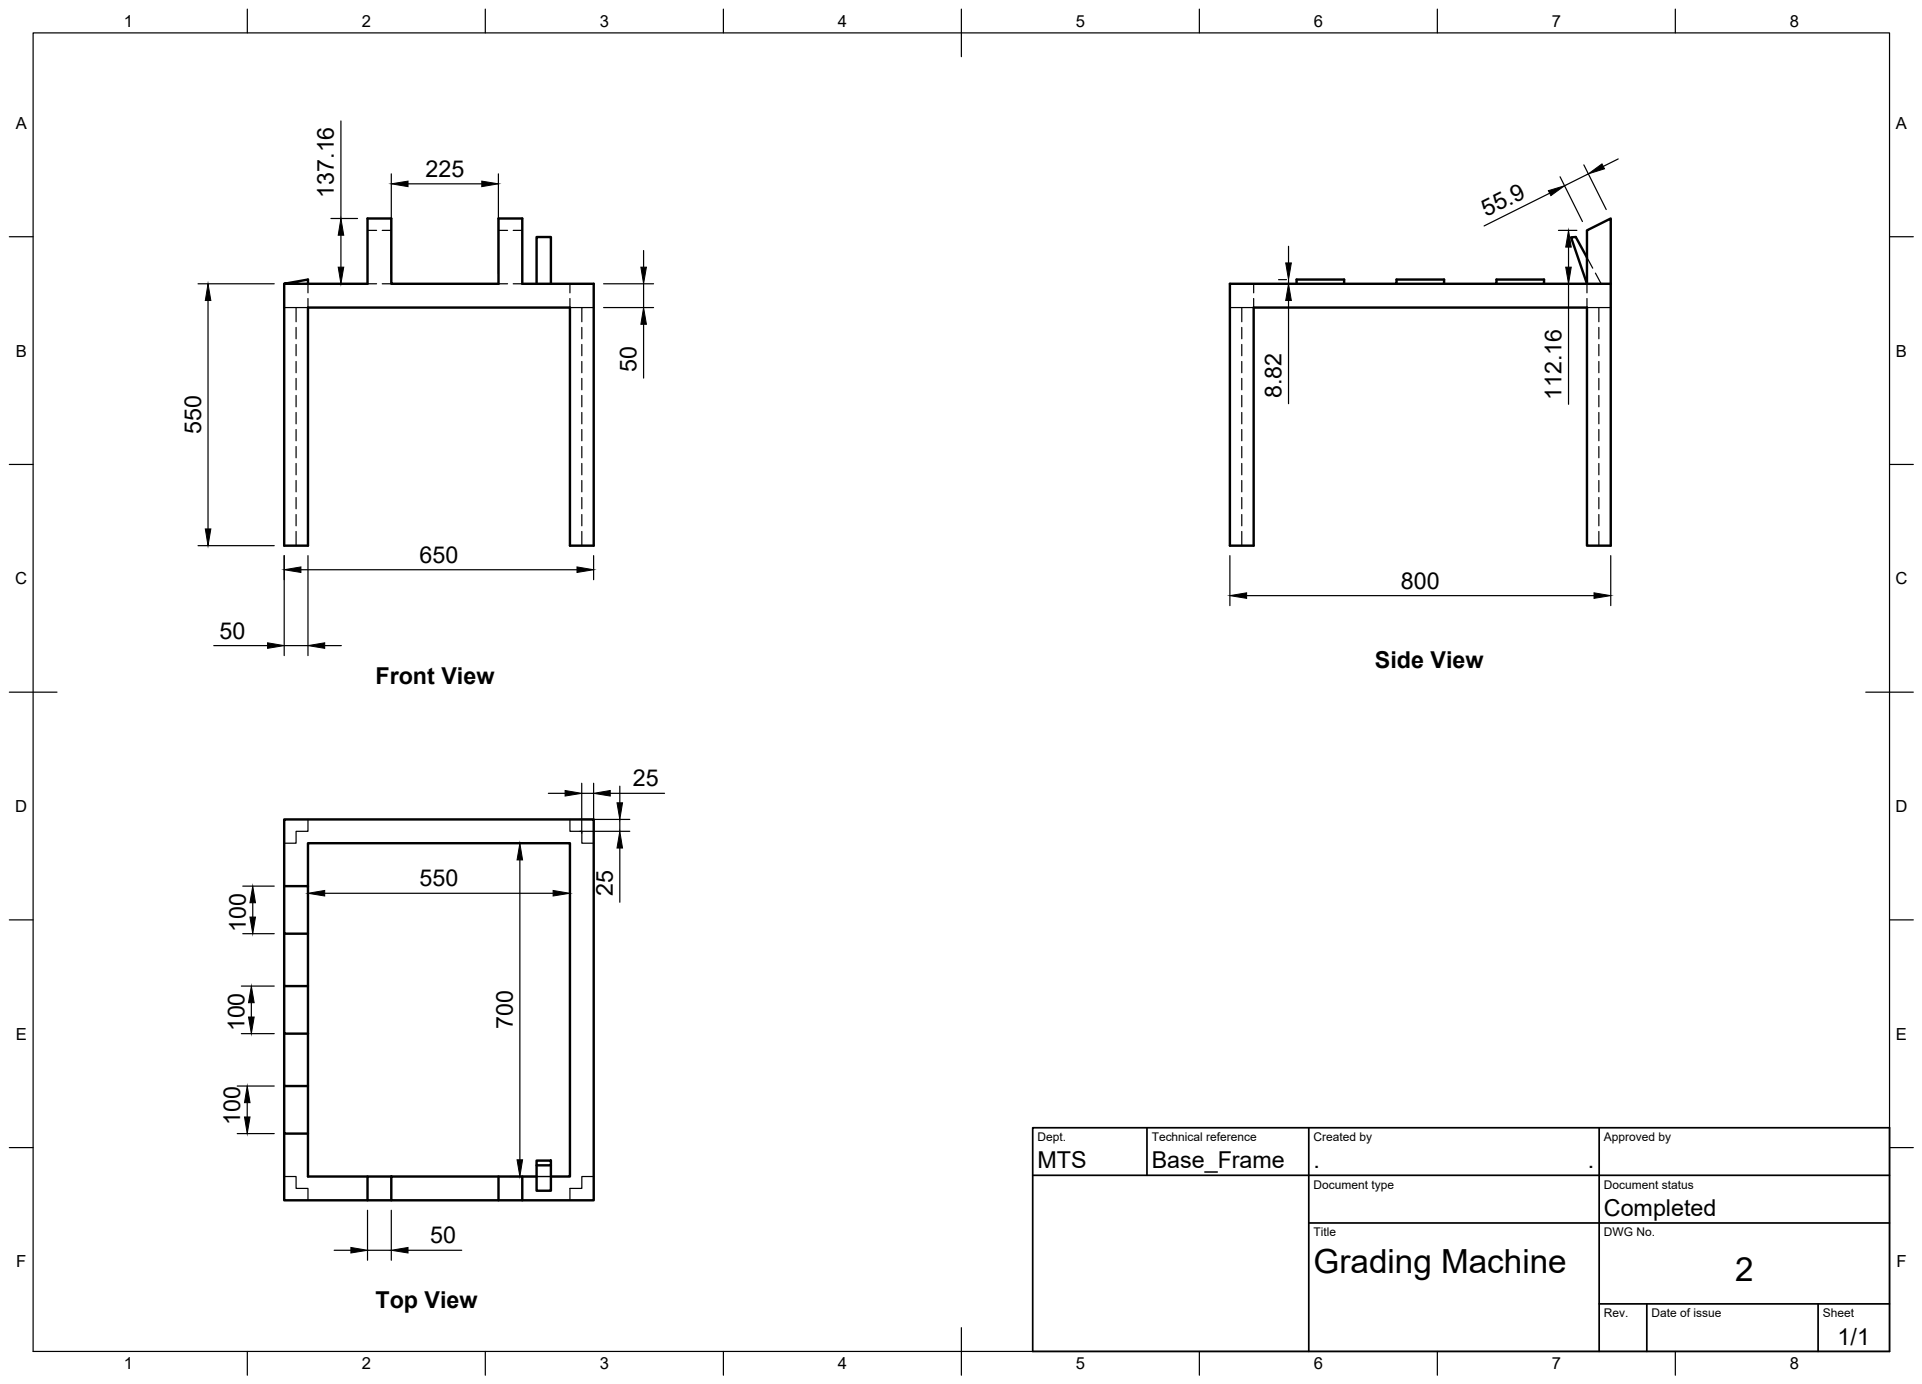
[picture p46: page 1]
Title; DWG No.; Rev.; Date of issue; Sheet; Grading Machine; MTS; Base_Frame; Front View; Top View; Side View

Dept. | Technical reference | Created by . | Approved by

Document type | Document status Completed

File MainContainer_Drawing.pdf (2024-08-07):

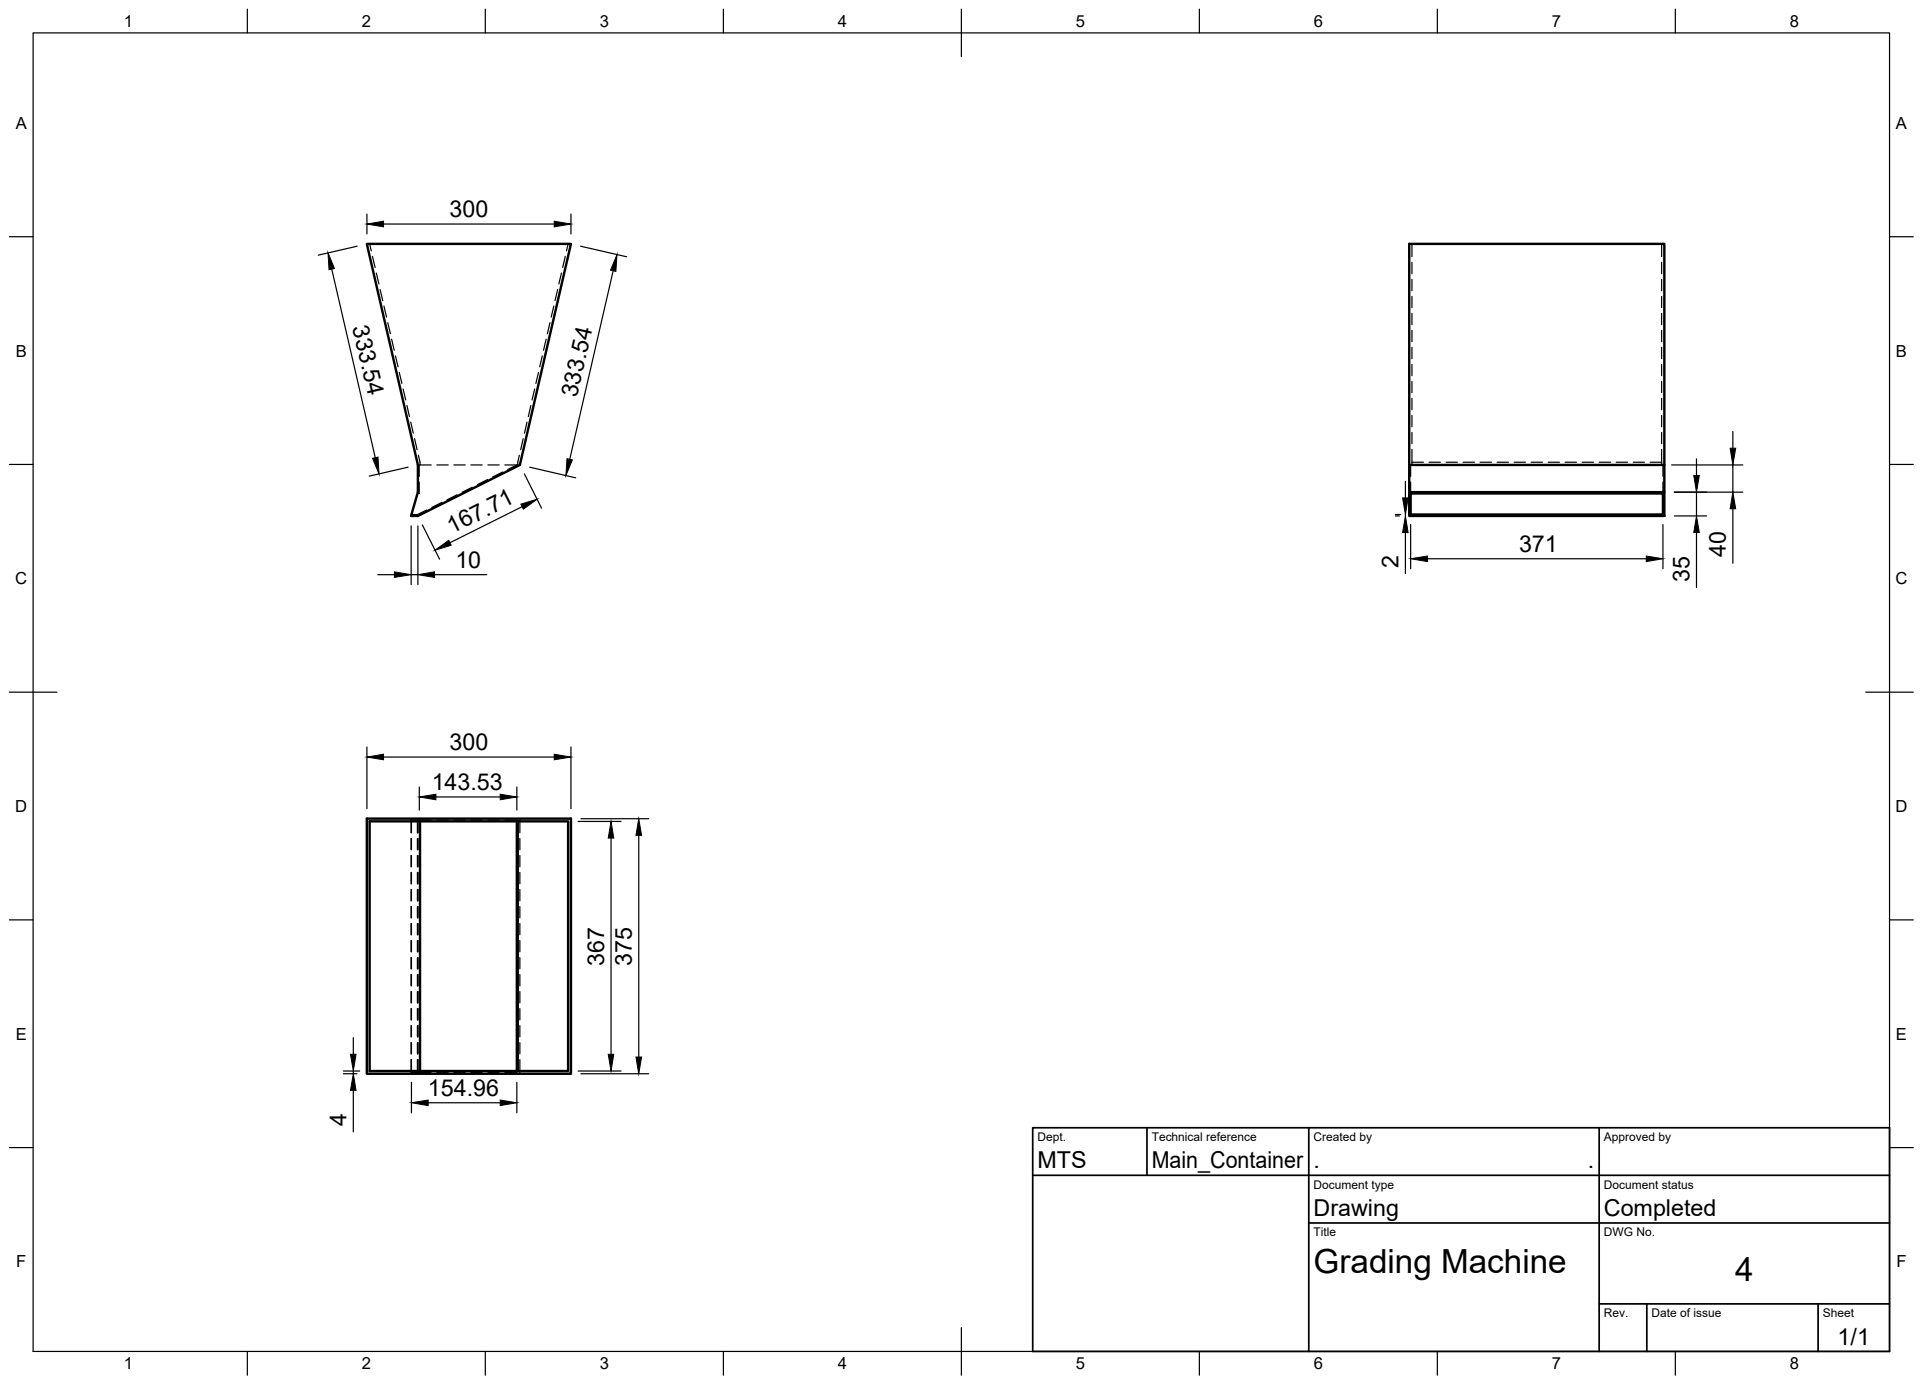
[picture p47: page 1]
Title; DWG No.; Rev.; Date of issue; Sheet; Grading Machine

Dept. MTS | Technical reference Main_Container | Created by . . | Approved by

Document type Drawing | Document status Completed

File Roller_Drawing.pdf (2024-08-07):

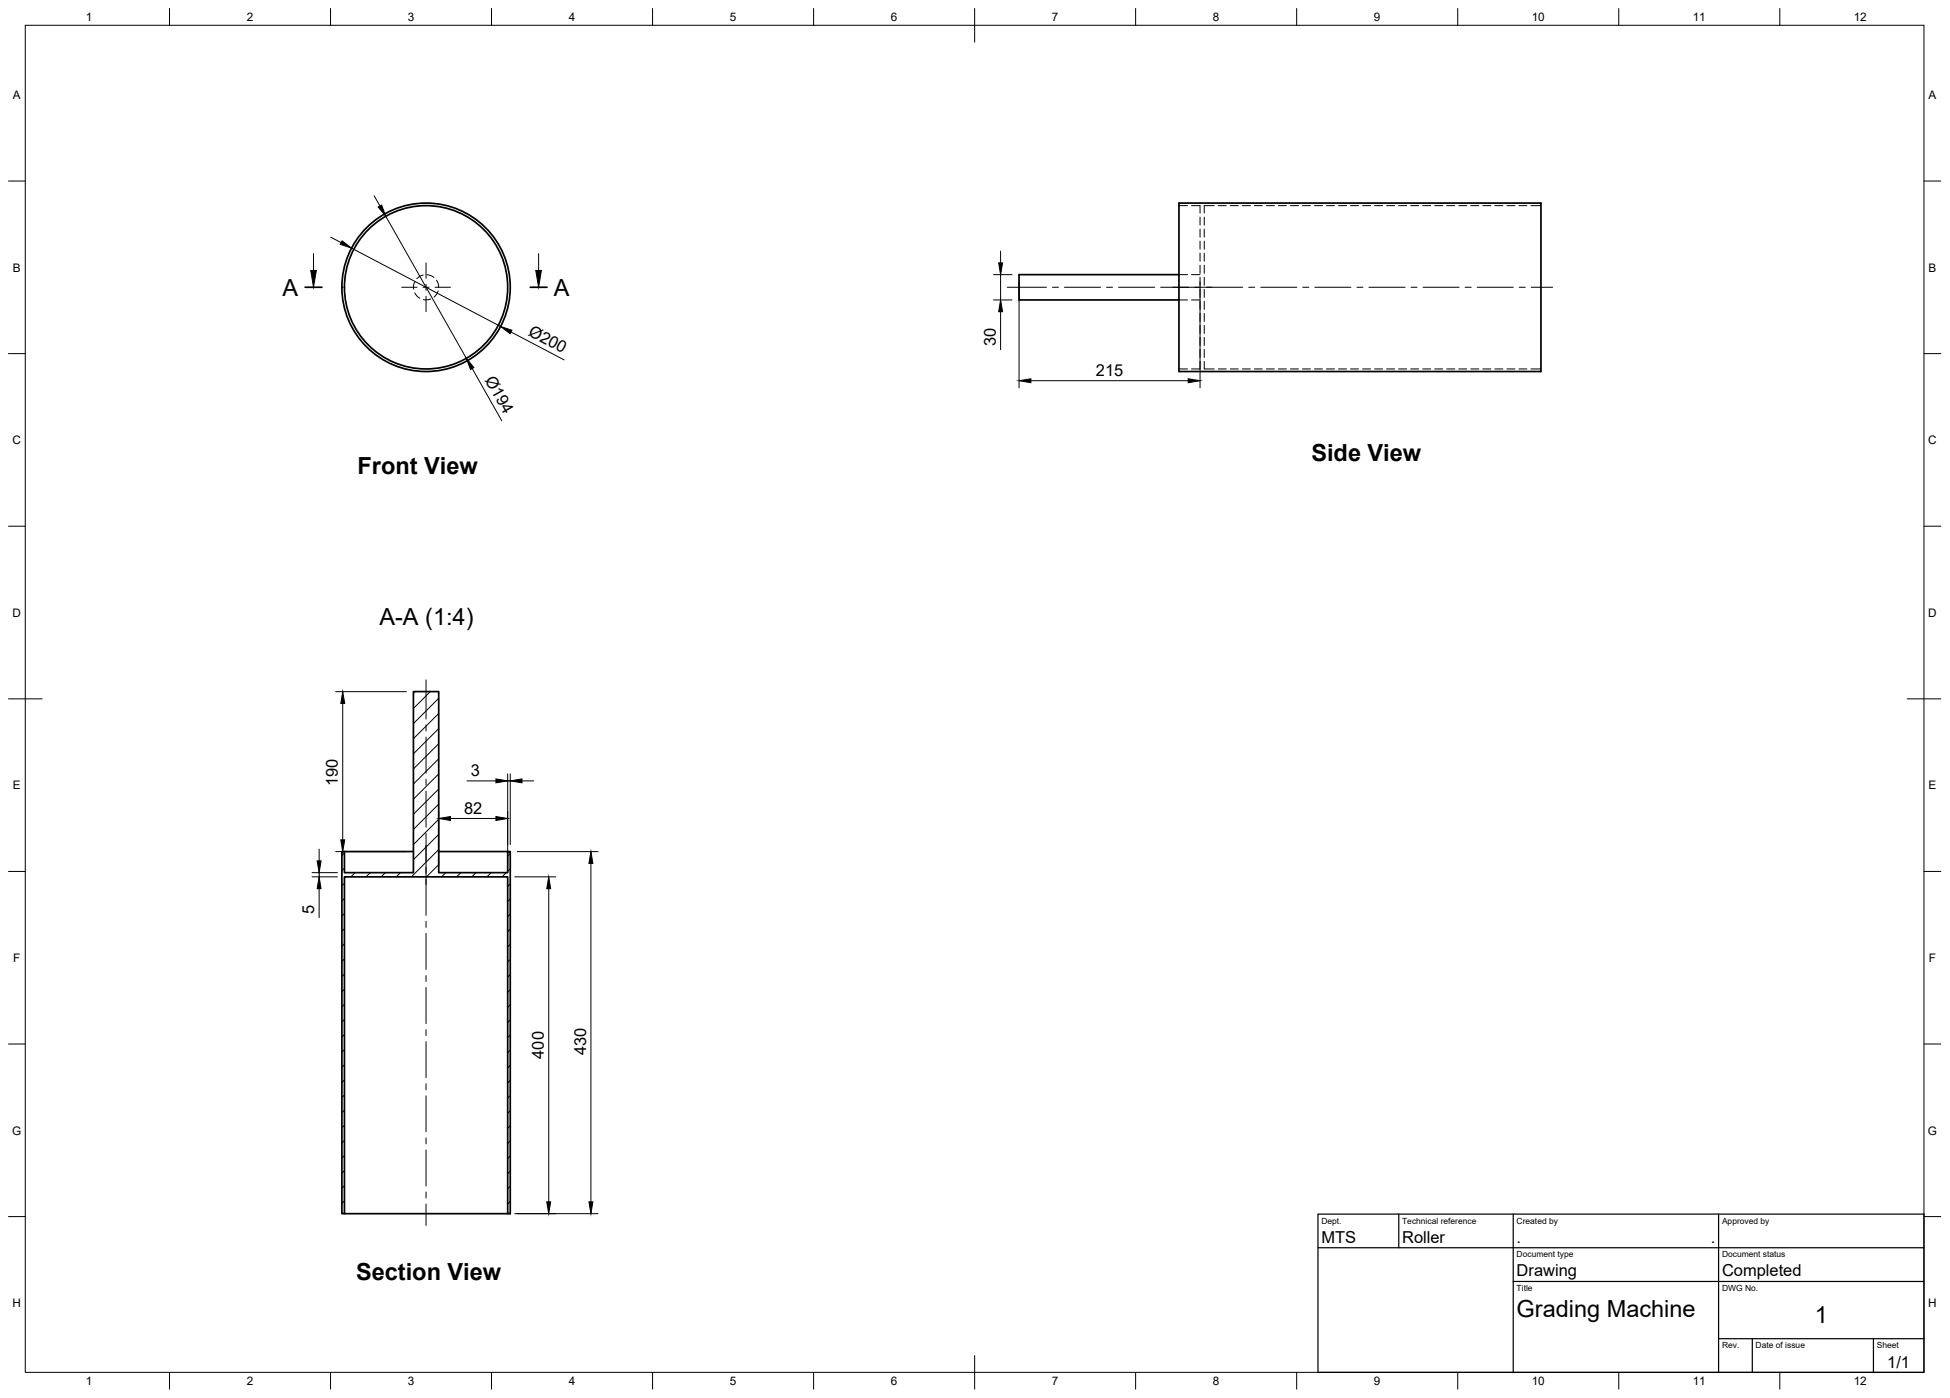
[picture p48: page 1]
Front View; Side View; Section View

Dept. MTS | Technical reference Roller | Created by . . | Approved by

Document type Drawing | Document status Completed

Title Grading Machine | DWG No. 1

Rev. | Date of issue | Sheet 1/1
